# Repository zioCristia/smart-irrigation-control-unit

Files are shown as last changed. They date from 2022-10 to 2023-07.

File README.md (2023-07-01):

# Smart irrigation expansion board
Expansion board for garden irrigation, with 7 differents triacs controlling solenoid valvs and one relay for the water pump.
This board should be attached to the [Esp energy monitor](https://github.com/zioCristia/esp-energy-monitor-v2) board.

You can watch an italian video tutorial throught [this link](https://youtu.be/GwXOpy07zA8).

Should one not need the power monitor, the board could be constructed by eliminating all components related to current measurement, thus leaving only the power supply and esp32.

The board's design allows it to be inserted into the rail of the home's breaker box by printing a 3D component.

The card can be divided into three sub-parts:
* The control of the 24V ac irrigation solenoid valves.
* The control of the water pump (maximum relay 16A).
* The control of the house electric gate from 12V dc.
  
## Table of contents
* [Hardware](#hardware)
* [Software](#software)
* [Pcb](#pcb)
* [Contribution](#contribution)

# Hardware
Each part of the card is independent of the others and can be omitted during construction if there is no need for it.
Similarly, you have the option of controlling 7 irrigation solenoid valves, but you can use a smaller number if you wish.
In this way, the price can vary (in particular reduce) drastically.

A complete list of all the components with a link to aliexpress could be found [here](https://docs.google.com/spreadsheets/d/1A_0oTcwCHzUrwPyKvZikXxDFFEQyVeJslgch1jBqpY8/edit?usp=sharing). The price is very indicative because if you already have components such as resistors or capacitors, it is drastically reduced.

### Additional hardware
For the installation of the board in the house panel directly into standard DIN rails, you can print two clips that you can find on [thingiverse](https://www.thingiverse.com/thing:6103419).

# Software
Esp32 was programmed using EspHome to enable its integration with [Home Assistant](https://www.home-assistant.io). To control solenoid valves, as well as the water pump and gate, simply add the following lines in the EspHome generic code for an esp32.
This will create them as switches in Home Assistant.

For more information, see the example code on the [energy monitor v2](https://github.com/zioCristia/esp-energy-monitor-v2/tree/main#software) or the [EspHome documentation](https://esphome.io).

```
switch:
  - platform: gpio
    name: "Cancello grande interruttore"
    pin: 
      number: GPIO19
      #inverted: true
    id: rele_cancello
    on_turn_on:
    - delay: 500ms
    - switch.turn_off: rele_cancello
    
  - platform: gpio
    pin: GPIO18
    name: "Pompa acqua"
    id: water_pump_switch
    #inverted: true
    restore_mode: ALWAYS_OFF
    
  - platform: gpio
    pin: GPIO15
    name: "irr1"
    id: irr1_switch
    inverted: true
    restore_mode: ALWAYS_OFF
    
  - platform: gpio
    pin: GPIO4
    name: "irr2"
    id: irr2_switch
    inverted: true
    restore_mode: ALWAYS_OFF
    
  - platform: gpio
    pin: GPIO16
    name: "irr3"
    id: irr3_switch
    inverted: true
    restore_mode: ALWAYS_OFF
    
  - platform: gpio
    pin: GPIO17
    name: "irr4"
    id: irr4_switch
    inverted: true
    restore_mode: ALWAYS_OFF
    
  - platform: gpio
    pin: GPIO14
    name: "irr5"
    id: irr5_switch
    inverted: true
    restore_mode: ALWAYS_OFF
    
  - platform: gpio
    pin: GPIO5
    name: "irr7"
    id: irr7_switch
    inverted: true
    restore_mode: ALWAYS_OFF
```

# Pcb
You can find the whole eagle project in [this folder](./irrigation_control_unit).
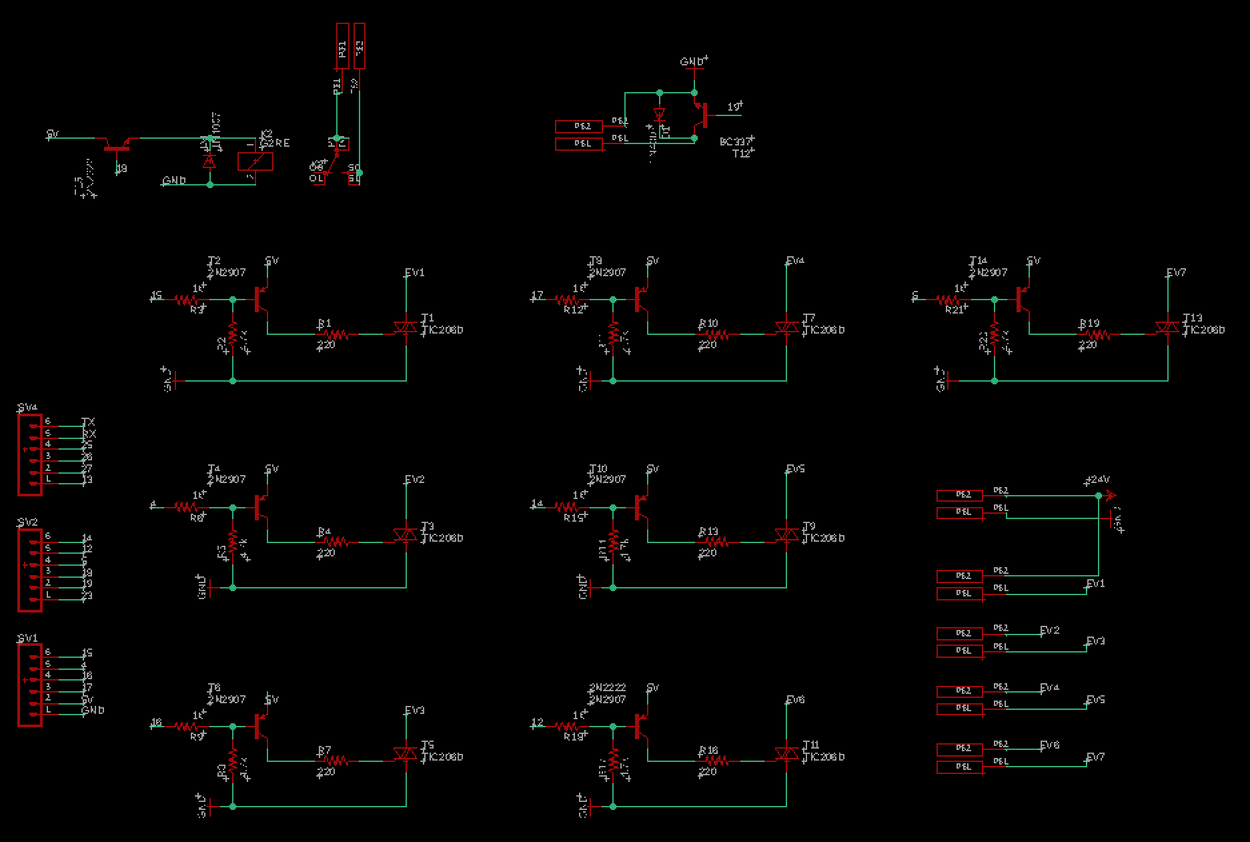
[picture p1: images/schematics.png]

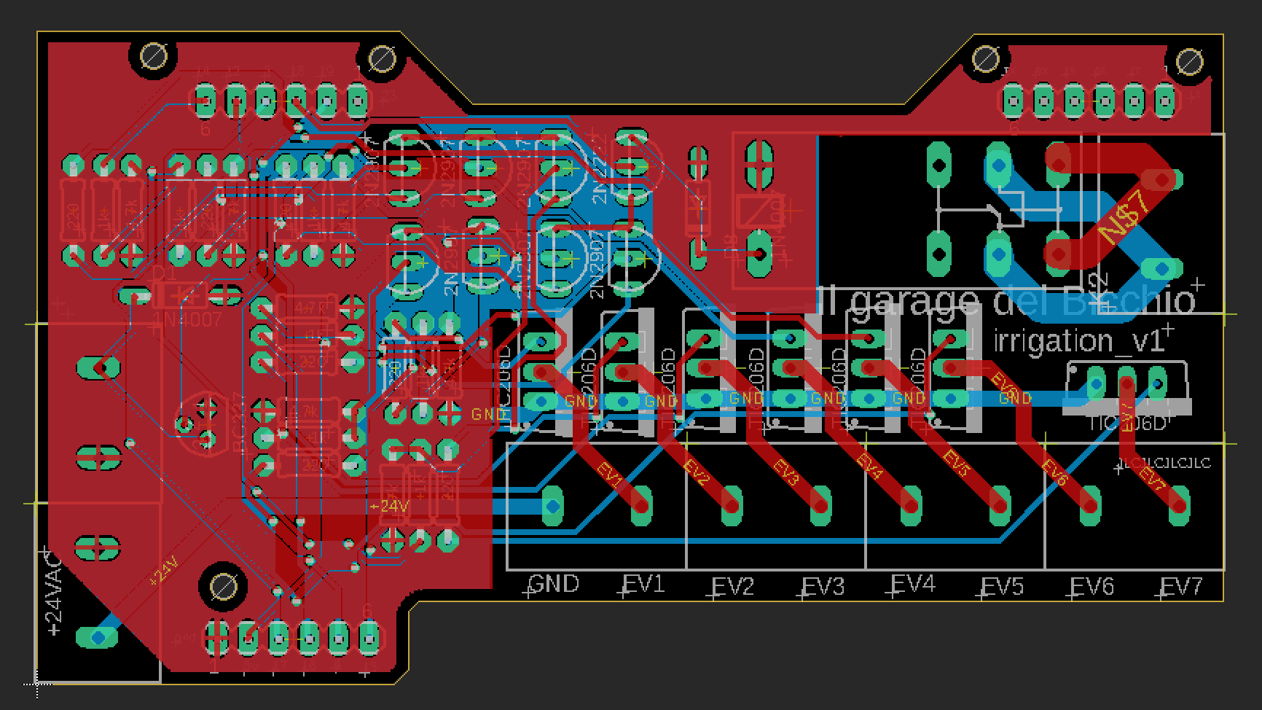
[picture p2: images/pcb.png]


# Contribution

Feel free to report any bugs or feature requests.

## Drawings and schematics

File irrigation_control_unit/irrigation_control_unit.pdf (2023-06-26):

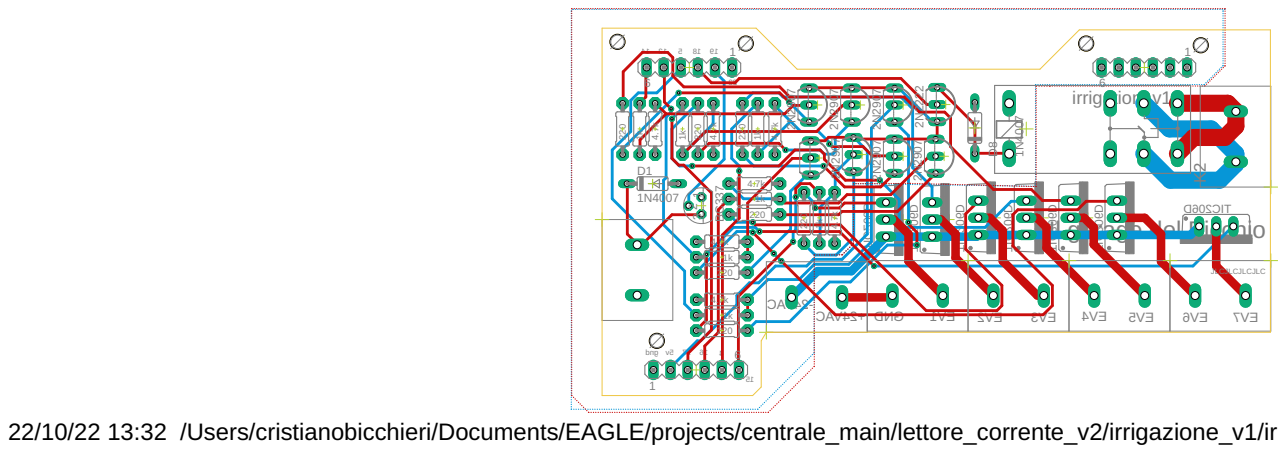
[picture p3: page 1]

TIC206D
Il garage del Bicchio

22/10/22 13:32 /Users/cristianobicchieri/Documents/EAGLE/projects/centrale_main/lettore_corrente_v2/irrigazione_v1/irr

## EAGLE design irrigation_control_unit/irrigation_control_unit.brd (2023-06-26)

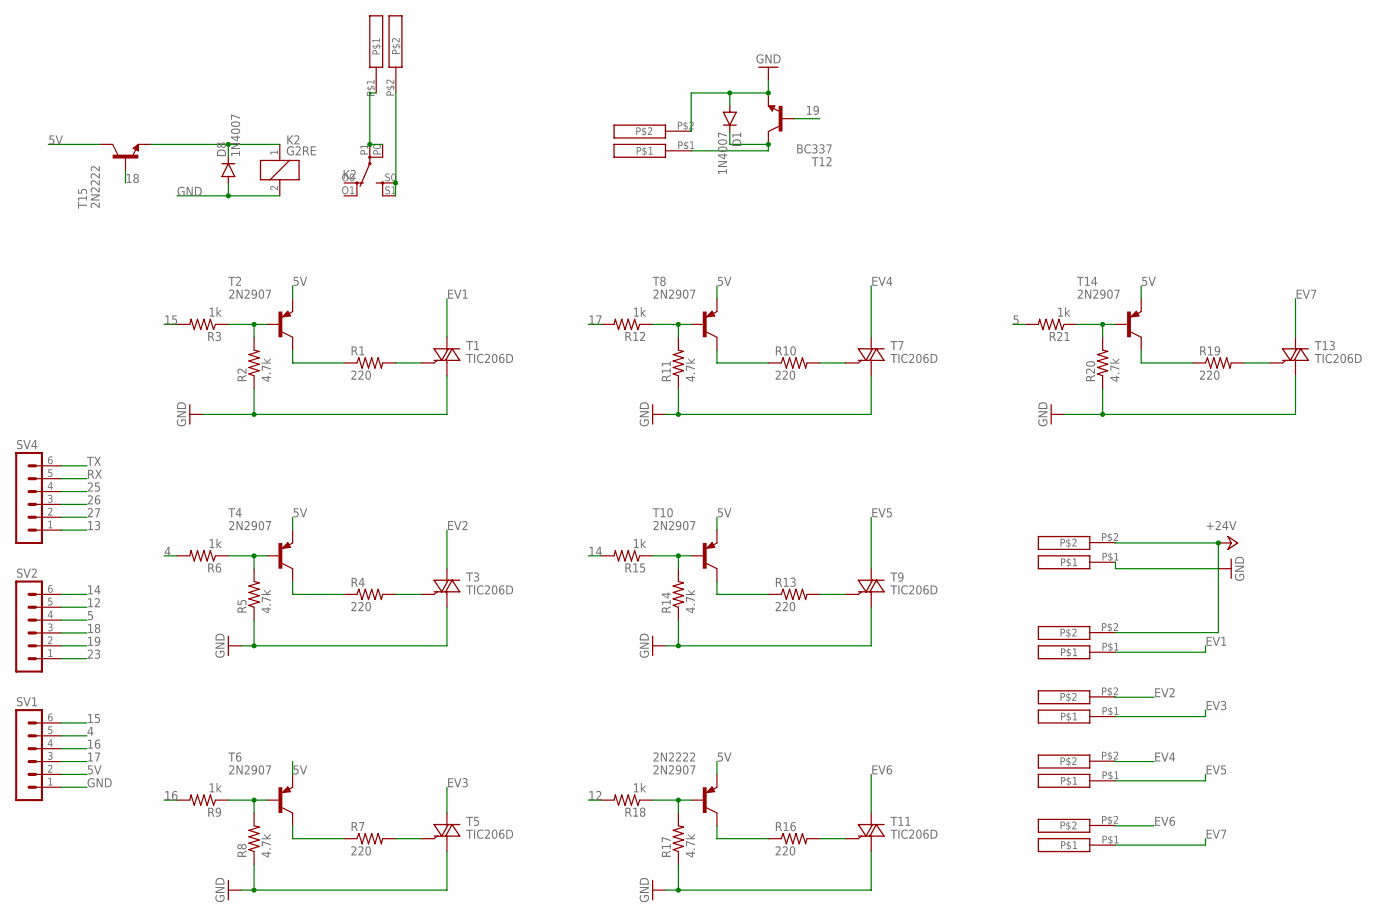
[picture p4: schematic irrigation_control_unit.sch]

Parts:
2N2222: 2N2907; TO92-EBC-OVAL
D1, D8: 1N4007; DO35-7
K2: G2RE
R1, R4, R7, R10, R13, R16, R19: 220; 0204/7
R2, R5, R8, R11, R14, R17, R20: 4.7k; 0204/7
R3, R6, R9, R12, R15, R18, R21: 1k; 0204/7
SV1, SV2, SV4: MA06-1
T1, T3, T5, T7, T9, T11, T13: TIC206D; TO220BV
T2, T4, T6, T8, T10, T14: 2N2907; TO92-EBC-OVAL
T12: BC337; TO92
T15: 2N2222; TO92-EBC-OVAL
U$1, U$2, U$3, U$4, U$5, U$6, U$7: 2-PIN-7.5-CONNECTOR

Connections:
4: R6.2, SV1.5
5: R21.2, SV2.4
5V: 2N2222.E, SV1.2, T2.E, T4.E, T6.E, T8.E, T10.E, T14.E, T15.C
12: R18.2, SV2.5
13: SV4.1
14: R15.2, SV2.6
15: R3.2, SV1.6
16: R9.2, SV1.4
17: R12.2, SV1.3
18: SV2.3, T15.B
19: SV2.2, T12.2 (B)
23: SV2.1
25: SV4.4
26: SV4.3
27: SV4.2
+24V: U$1.P$2, U$2.P$2
EV1: T1.T2 (A2), U$2.P$1
EV2: T3.T2 (A2), U$3.P$2
EV3: T5.T2 (A2), U$3.P$1
EV4: T7.T2 (A2), U$4.P$2
EV5: T9.T2 (A2), U$4.P$1
EV6: T11.T2 (A2), U$5.P$2
EV7: T13.T2 (A2), U$5.P$1
GND: D1.A, D8.A, K2.2, R2.1, R5.1, R8.1, R11.1, R14.1, R17.1, R20.1, SV1.1, T1.T1 (A1), T3.T1 (A1), T5.T1 (A1), T7.T1 (A1), T9.T1 (A1), T11.T1 (A1), T12.1 (E), T13.T1 (A1), U$1.P$1, U$7.P$2
unnamed: D8.C, K2.1, T15.E
unnamed: R1.2, T1.G
unnamed: R1.1, T2.C
unnamed: D1.C, T12.3 (C), U$7.P$1
unnamed: R2.2, R3.1, T2.B
unnamed: K2.P0, K2.P1, U$6.P$1
unnamed: K2.S0 (S), K2.S1 (S), U$6.P$2
unnamed: R4.2, T3.G
unnamed: R4.1, T4.C
unnamed: R5.2, R6.1, T4.B
unnamed: R7.2, T5.G
unnamed: R7.1, T6.C
unnamed: R8.2, R9.1, T6.B
unnamed: R10.2, T7.G
unnamed: R10.1, T8.C
unnamed: R11.2, R12.1, T8.B
unnamed: R13.2, T9.G
unnamed: R13.1, T10.C
unnamed: R14.2, R15.1, T10.B
unnamed: R16.2, T11.G
unnamed: 2N2222.C, R16.1
unnamed: 2N2222.B, R17.2, R18.1
unnamed: R19.2, T13.G
unnamed: R19.1, T14.C
unnamed: R20.2, R21.1, T14.B
RX: SV4.5
TX: SV4.6

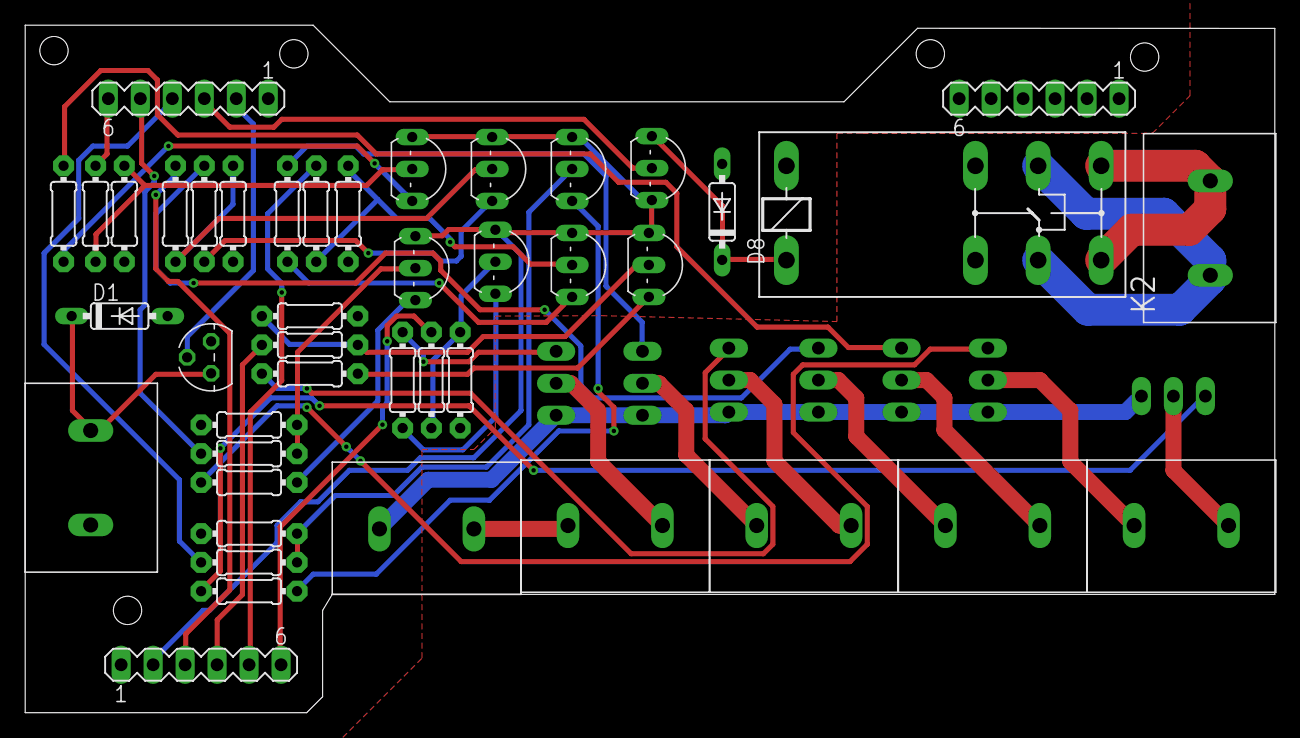
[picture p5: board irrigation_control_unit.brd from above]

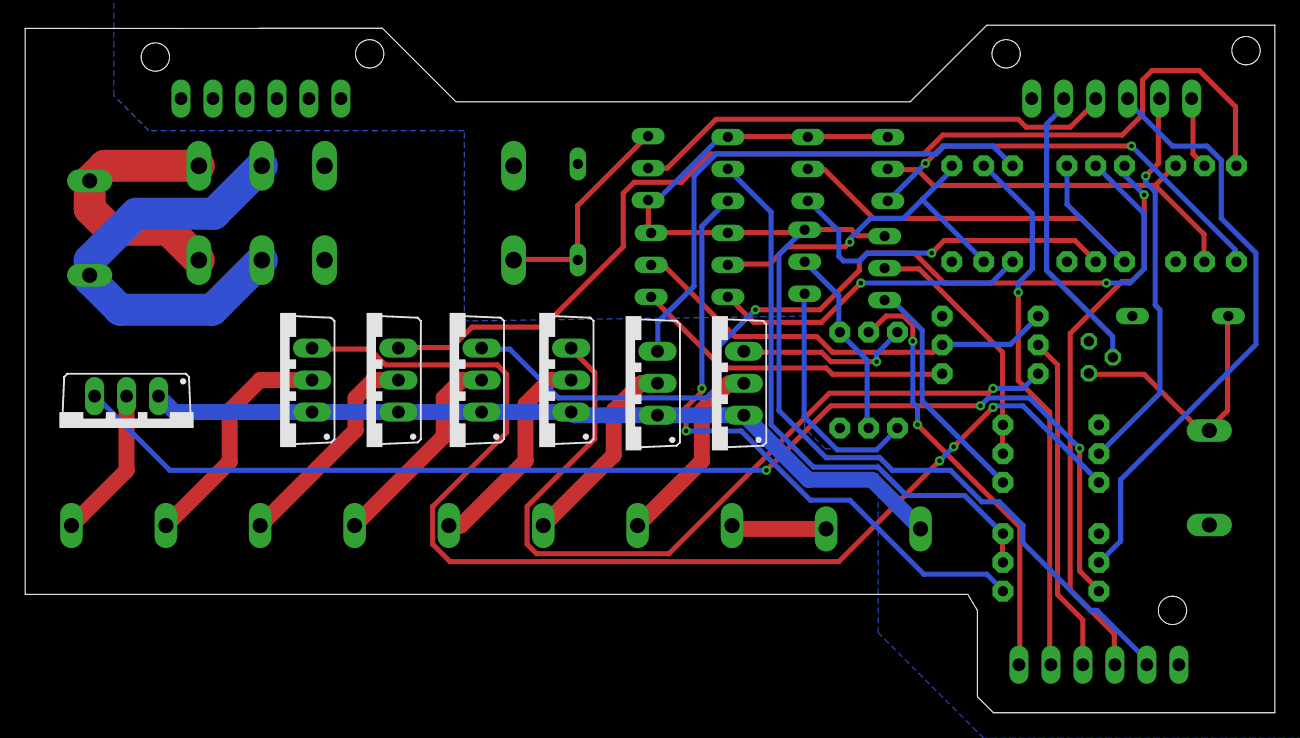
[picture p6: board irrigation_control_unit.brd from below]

Board: 2 copper layers, 99.2 x 54.6 mm, 50 parts (7 on the bottom side), 44 nets.
